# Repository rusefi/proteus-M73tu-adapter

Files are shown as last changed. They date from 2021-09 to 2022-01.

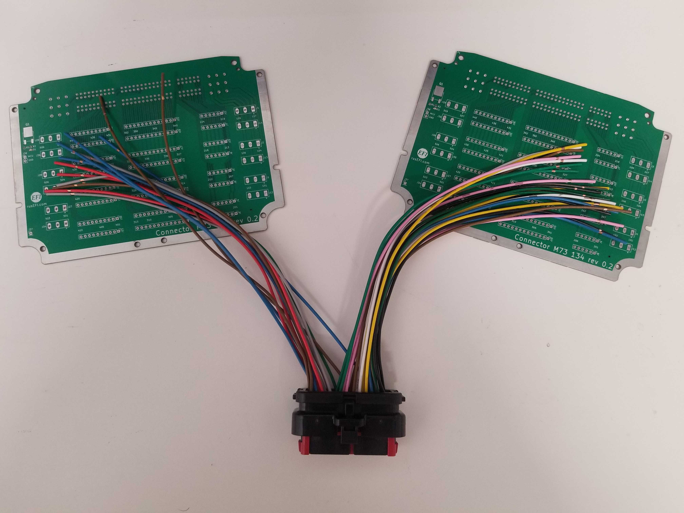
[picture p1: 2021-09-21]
todo/adapter-proto.jpg

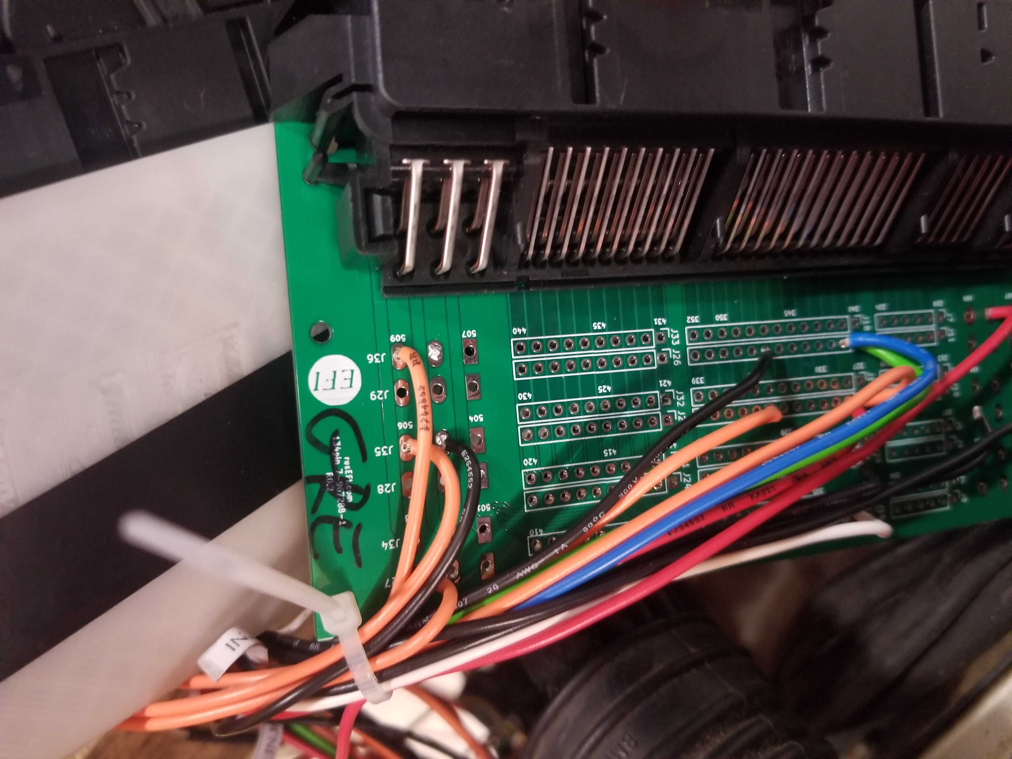
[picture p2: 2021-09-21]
todo/manual_wiring.jpg

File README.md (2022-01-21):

# proteus-m73tu-adapter

Part of https://github.com/rusefi/rusefi/wiki/Proteus#adapters family

https://github.com/mck1117/proteus meets https://github.com/rusefi/rusefi/wiki/HOWTO-M73-v12-on-Proteus

V12 harness uses _TWO_ 134 pin connectors - one with BLACK plugs another with GREY plugs.

x

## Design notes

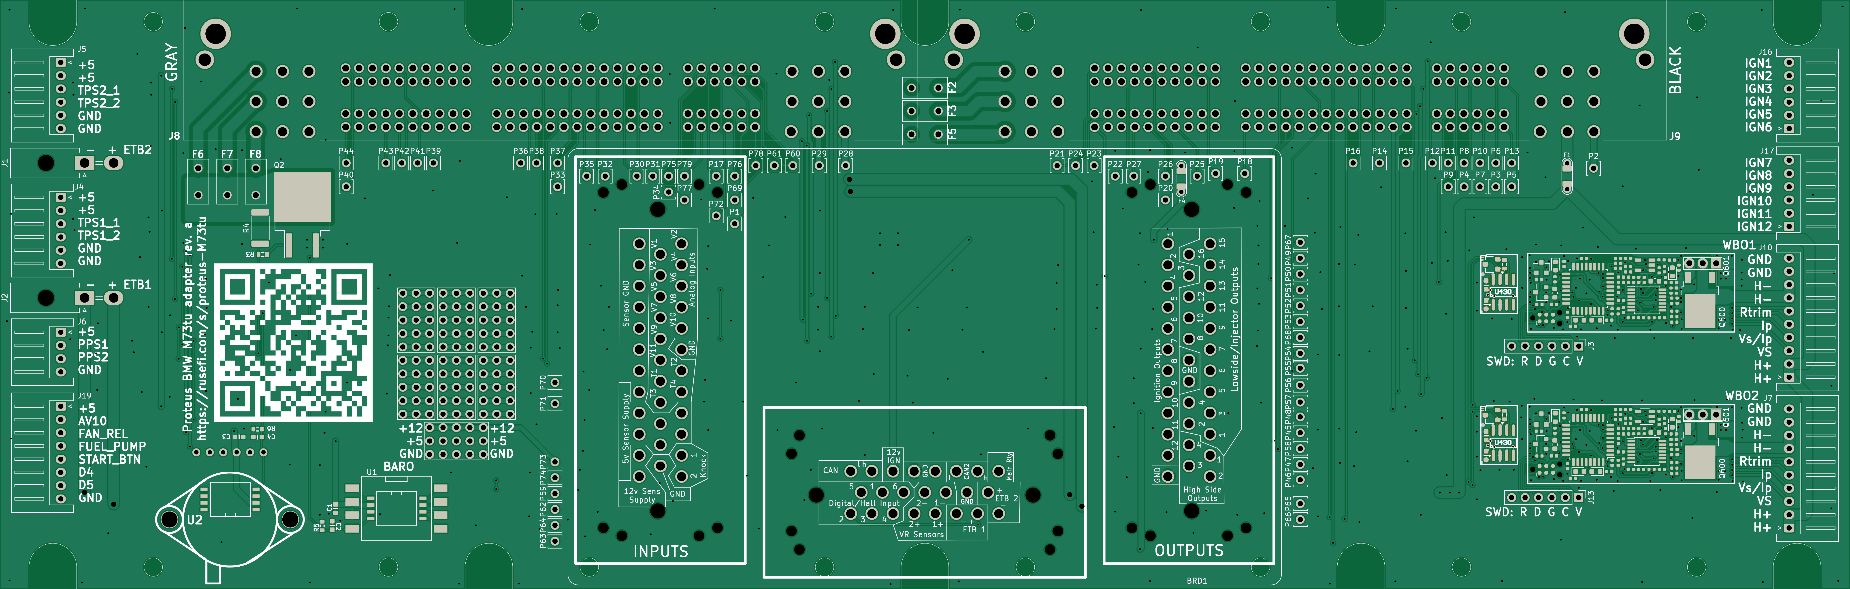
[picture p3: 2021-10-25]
proteusM73tu/boards/proteusM73tu-a/board/misc/proteusM73tu-a-top.png

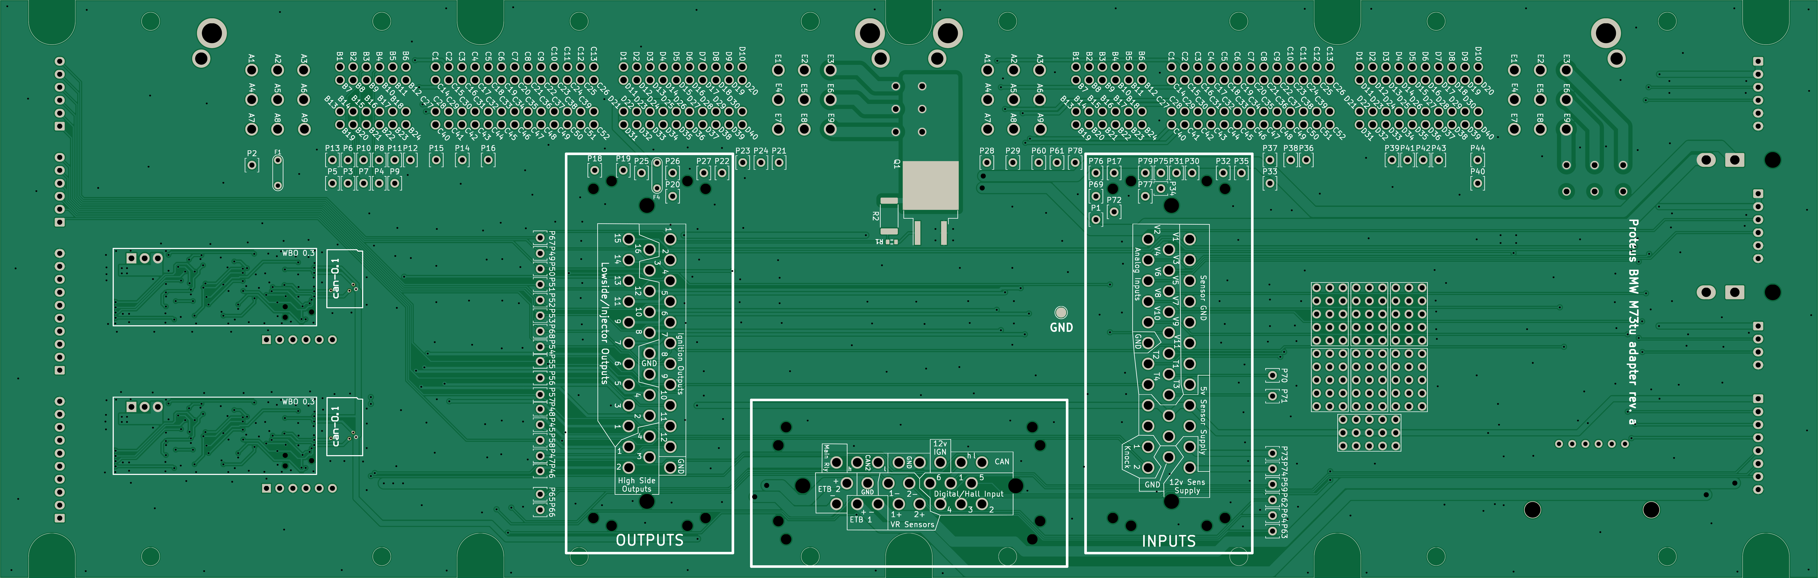
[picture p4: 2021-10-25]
proteusM73tu/boards/proteusM73tu-a/board/misc/proteusM73tu-a-bottom.png

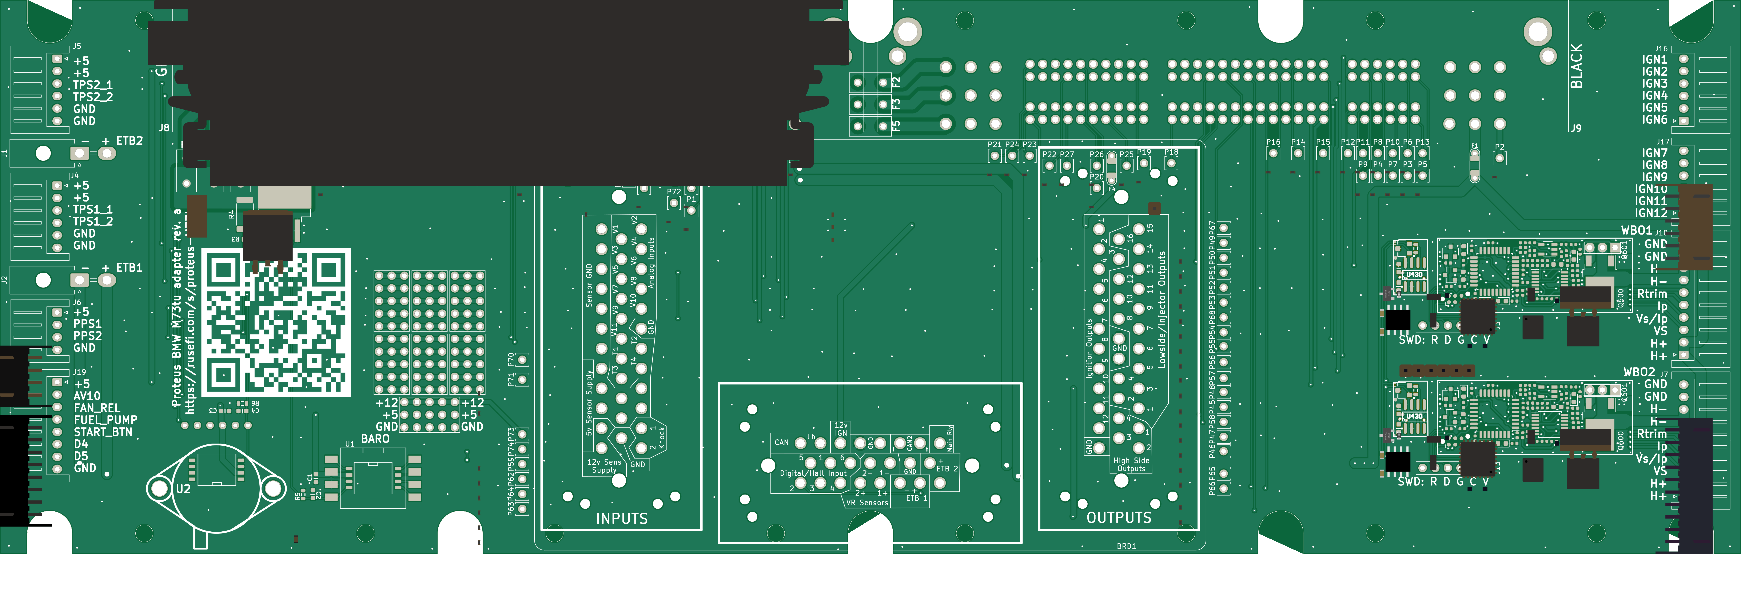
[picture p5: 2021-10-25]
proteusM73tu/boards/proteusM73tu-a/board/proteusM73tu-a.png

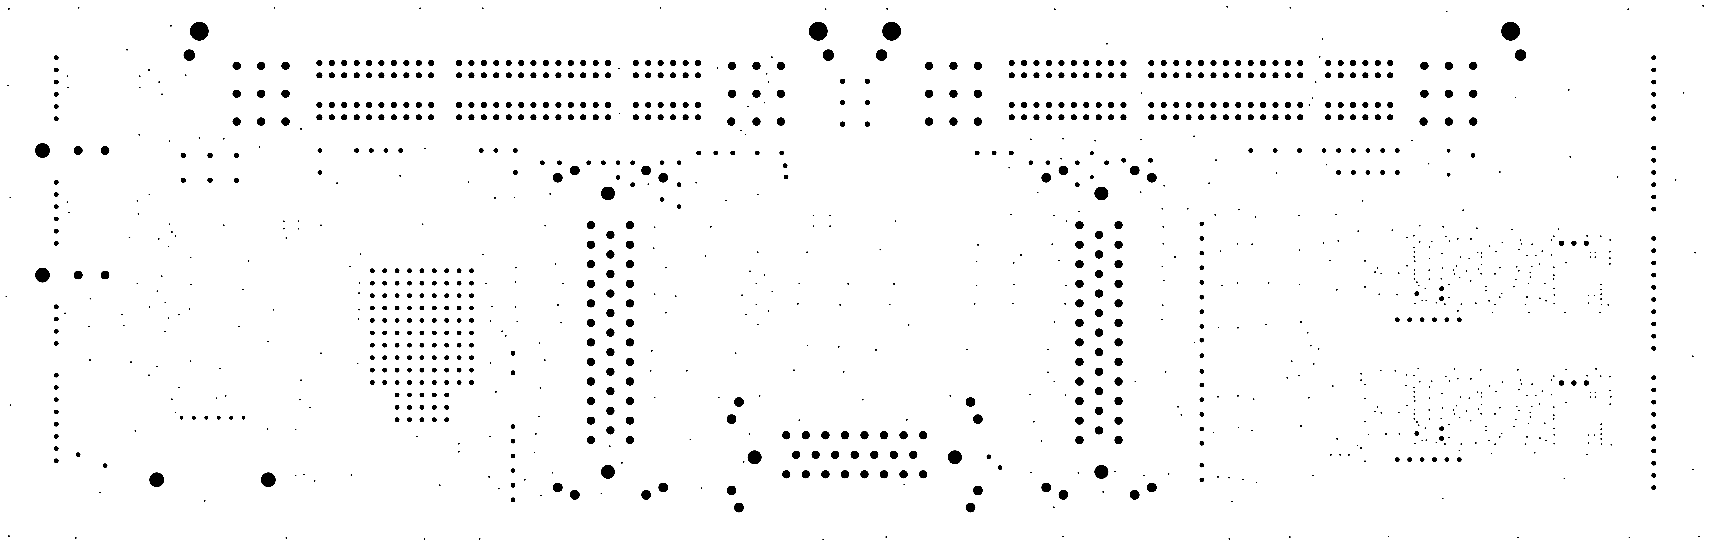
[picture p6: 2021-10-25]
proteusM73tu/boards/proteusM73tu-a/board/misc/proteusM73tu-a-outline.png

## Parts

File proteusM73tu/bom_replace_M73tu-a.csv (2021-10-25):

#WBO low-side (D2PAK | TO220)
Q600
Q600_2
Q601
Q601_2
#WBO STM32
U602
U602_2
#IGN IGBT
Q1 | ISL9V3040D3ST | DPAK | NON-JLC
Q2 | ISL9V3040D3ST | DPAK | NON-JLC
#MPX | MAP
U1
U2

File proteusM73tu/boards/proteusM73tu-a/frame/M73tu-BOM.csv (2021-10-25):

Comment | Designator | Footprint | LCSC Part #
proteus | BRD1 | proteus
100n | C1 | C0603 | C14663
47p | C2 | C0603 | C1671
100n | C3 | C0603 | C14663
47p | C4 | C0603 | C1671
Fuse-Pad-Pad | F1 | PAD-1206-PAD | C182446
10A | F2 | FUSE_8.5x4 | C354908
10A | F3 | FUSE_8.5x4 | C354908
Fuse-Pad-Pad | F4 | PAD-1206-PAD | C182446
10A | F5 | FUSE_8.5x4 | C354908
10A | F6 | FUSE_8.5x4 | C354908
10A | F7 | FUSE_8.5x4 | C354908
10A | F8 | FUSE_8.5x4 | C354908
PROTO_AREA | G1 | PROTO_AREA
PROTO_AREA | G2 | PROTO_AREA
PROTO_AREA | G3 | PROTO_AREA
PROTO_AREA | G4 | PROTO_AREA
PROTO_AREA | G5 | PROTO_AREA
PROTO_AREA | G6 | PROTO_AREA
PROTO_AREA | G7 | PROTO_AREA
Conn_01x02 | J1 | Molex_Mini-Fit_Jr_5569-02A2_2x01_P4.20mm_Horizontal | C240832
Conn_01x02 | J2 | Molex_Mini-Fit_Jr_5569-02A2_2x01_P4.20mm_Horizontal | C240832
Conn_01x06 | J3 | PinHeader_1x06_P2.54mm_Vertical
XH-6AW | J4 | JST_XH_S6B-XH-A_1x06_P2.50mm_Horizontal | C8876
XH-6AW | J5 | JST_XH_S6B-XH-A_1x06_P2.50mm_Horizontal | C8876
XH-4AW | J6 | JST_XH_S4B-XH-A_1x04_P2.50mm_Horizontal | C21273
XH-10AW | J7 | JST_XH_S10B-XH-A_1x10_P2.50mm_Horizontal | C14652
7-967288-1 | J8 | TE_7-967288-1
7-967288-1 | J9 | TE_7-967288-1
XH-10AW | J10 | JST_XH_S10B-XH-A_1x10_P2.50mm_Horizontal | C14652
Conn_01x06 | J13 | PinHeader_1x06_P2.54mm_Vertical
XH-6AW | J16 | JST_XH_S6B-XH-A_1x06_P2.50mm_Horizontal | C8876
XH-6AW | J17 | JST_XH_S6B-XH-A_1x06_P2.50mm_Horizontal | C8876
XH-8AW | J19 | JST_XH_S8B-XH-A_1x08_P2.50mm_Horizontal | C10395
Conn_01x01 | J20 | TestPoint_Pad_D2.0mm
Module:wbo/0.3 | M1 | wbo
Module:can/0.1 | M2 | can
Module:wbo/0.3 | M3 | wbo
Module:can/0.1 | M4 | can
Pad | P1 | PAD-TH
Pad | P2 | PAD-TH
Pad | P3 | PAD-TH
Pad | P4 | PAD-TH
Pad | P5 | PAD-TH
Pad | P6 | PAD-TH
Pad | P7 | PAD-TH
Pad | P8 | PAD-TH
Pad | P9 | PAD-TH
Pad | P10 | PAD-TH
Pad | P11 | PAD-TH
Pad | P12 | PAD-TH
Pad | P13 | PAD-TH
Pad | P14 | PAD-TH
Pad | P15 | PAD-TH
Pad | P16 | PAD-TH
Pad | P17 | PAD-TH
Pad | P18 | PAD-TH
Pad | P19 | PAD-TH
Pad | P20 | PAD-TH
Pad | P21 | PAD-TH
Pad | P22 | PAD-TH
Pad | P23 | PAD-TH
Pad | P24 | PAD-TH
Pad | P25 | PAD-TH
Pad | P26 | PAD-TH
Pad | P27 | PAD-TH
Pad | P28 | PAD-TH
Pad | P29 | PAD-TH
Pad | P30 | PAD-TH
Pad | P31 | PAD-TH
Pad | P32 | PAD-TH
Pad | P33 | PAD-TH
Pad | P34 | PAD-TH
Pad | P35 | PAD-TH
Pad | P36 | PAD-TH
Pad | P37 | PAD-TH
Pad | P38 | PAD-TH
Pad | P39 | PAD-TH
Pad | P40 | PAD-TH
Pad | P41 | PAD-TH
Pad | P42 | PAD-TH
Pad | P43 | PAD-TH
Pad | P44 | PAD-TH
Pad | P45 | PAD-TH
Pad | P46 | PAD-TH
Pad | P47 | PAD-TH
Pad | P48 | PAD-TH
Pad | P49 | PAD-TH
Pad | P50 | PAD-TH
Pad | P51 | PAD-TH
Pad | P52 | PAD-TH
Pad | P53 | PAD-TH
Pad | P54 | PAD-TH
Pad | P55 | PAD-TH
Pad | P56 | PAD-TH
Pad | P57 | PAD-TH
Pad | P58 | PAD-TH
Pad | P59 | PAD-TH
Pad | P60 | PAD-TH
Pad | P61 | PAD-TH
Pad | P62 | PAD-TH
Pad | P63 | PAD-TH
Pad | P64 | PAD-TH
Pad | P65 | PAD-TH
Pad | P66 | PAD-TH
Pad | P67 | PAD-TH
Pad | P68 | PAD-TH
Pad | P69 | PAD-TH
Pad | P70 | PAD-TH
Pad | P71 | PAD-TH
Pad | P72 | PAD-TH
Pad | P73 | PAD-TH
Pad | P74 | PAD-TH
Pad | P75 | PAD-TH
Pad | P76 | PAD-TH
Pad | P77 | PAD-TH
Pad | P78 | PAD-TH
Pad | P79 | PAD-TH
ISL9V3040S3S | Q1 | TO-263-2 | C898702
ISL9V3040S3S | Q2 | TO-263-2 | C898702
22 | R1 | R0603 | C23345
DNP | R2 | R_2512_6332Metric
22 | R3 | R0603 | C23345
DNP | R4 | R_2512_6332Metric
51k | R5 | R0603 | C23196
51k | R6 | R0603 | C23196
MPXxx6115A | U1 | MPX_SOP_SSOP
MPX4/MPXH6400_MAP | U2 | MPX-4_MAP

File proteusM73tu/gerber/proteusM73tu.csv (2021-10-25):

Comment | Designator | Footprint | LCSC Part #
proteus | BRD1 | kicad6-libraries:proteus
100n | C1 | hellen-one-common:C0603 | C14663
47p | C2 | hellen-one-common:C0603 | C1671
100n | C3 | hellen-one-common:C0603 | C14663
47p | C4 | hellen-one-common:C0603 | C1671
Fuse-Pad-Pad | F1 | hellen-one-common:PAD-1206-PAD | C182446
10A | F2 | kicad6-libraries:FUSE_8.5x4 | C354908
10A | F3 | kicad6-libraries:FUSE_8.5x4 | C354908
Fuse-Pad-Pad | F4 | hellen-one-common:PAD-1206-PAD | C182446
10A | F5 | kicad6-libraries:FUSE_8.5x4 | C354908
10A | F6 | kicad6-libraries:FUSE_8.5x4 | C354908
10A | F7 | kicad6-libraries:FUSE_8.5x4 | C354908
10A | F8 | kicad6-libraries:FUSE_8.5x4 | C354908
PROTO_AREA | G1 | hellen-one-common:PROTO_AREA
PROTO_AREA | G2 | hellen-one-common:PROTO_AREA
PROTO_AREA | G3 | hellen-one-common:PROTO_AREA
PROTO_AREA | G4 | hellen-one-common:PROTO_AREA
PROTO_AREA | G5 | hellen-one-common:PROTO_AREA
PROTO_AREA | G6 | hellen-one-common:PROTO_AREA
PROTO_AREA | G7 | hellen-one-common:PROTO_AREA
Conn_01x02 | J1 | Connector_Molex:Molex_Mini-Fit_Jr_5569-02A2_2x01_P4.20mm_Horizontal | C240832
Conn_01x02 | J2 | Connector_Molex:Molex_Mini-Fit_Jr_5569-02A2_2x01_P4.20mm_Horizontal | C240832
Conn_01x06 | J3 | Connector_PinHeader_2.54mm:PinHeader_1x06_P2.54mm_Vertical
XH-6AW | J4 | Connector_JST:JST_XH_S6B-XH-A_1x06_P2.50mm_Horizontal | C8876
XH-6AW | J5 | Connector_JST:JST_XH_S6B-XH-A_1x06_P2.50mm_Horizontal | C8876
XH-4AW | J6 | Connector_JST:JST_XH_S4B-XH-A_1x04_P2.50mm_Horizontal | C21273
XH-10AW | J7 | Connector_JST:JST_XH_S10B-XH-A_1x10_P2.50mm_Horizontal | C14652
7-967288-1 | J8 | kicad6-libraries:TE_7-967288-1
7-967288-1 | J9 | kicad6-libraries:TE_7-967288-1
XH-10AW | J10 | Connector_JST:JST_XH_S10B-XH-A_1x10_P2.50mm_Horizontal | C14652
Conn_01x06 | J13 | Connector_PinHeader_2.54mm:PinHeader_1x06_P2.54mm_Vertical
XH-6AW | J16 | Connector_JST:JST_XH_S6B-XH-A_1x06_P2.50mm_Horizontal | C8876
XH-6AW | J17 | Connector_JST:JST_XH_S6B-XH-A_1x06_P2.50mm_Horizontal | C8876
XH-8AW | J19 | Connector_JST:JST_XH_S8B-XH-A_1x08_P2.50mm_Horizontal | C10395
Conn_01x01 | J20 | TestPoint:TestPoint_Pad_D2.0mm
Module-wbo-0.3 | M1 | hellen-one-wbo-0.3:wbo
Module-can-0.1 | M2 | hellen-one-can-0.1:can
Module-wbo-0.3 | M3 | hellen-one-wbo-0.3:wbo
Module-can-0.1 | M4 | hellen-one-can-0.1:can
Pad | P1 | hellen-one-common:PAD-TH
Pad | P2 | hellen-one-common:PAD-TH
Pad | P3 | hellen-one-common:PAD-TH
Pad | P4 | hellen-one-common:PAD-TH
Pad | P5 | hellen-one-common:PAD-TH
Pad | P6 | hellen-one-common:PAD-TH
Pad | P7 | hellen-one-common:PAD-TH
Pad | P8 | hellen-one-common:PAD-TH
Pad | P9 | hellen-one-common:PAD-TH
Pad | P10 | hellen-one-common:PAD-TH
Pad | P11 | hellen-one-common:PAD-TH
Pad | P12 | hellen-one-common:PAD-TH
Pad | P13 | hellen-one-common:PAD-TH
Pad | P14 | hellen-one-common:PAD-TH
Pad | P15 | hellen-one-common:PAD-TH
Pad | P16 | hellen-one-common:PAD-TH
Pad | P17 | hellen-one-common:PAD-TH
Pad | P18 | hellen-one-common:PAD-TH
Pad | P19 | hellen-one-common:PAD-TH
Pad | P20 | hellen-one-common:PAD-TH
Pad | P21 | hellen-one-common:PAD-TH
Pad | P22 | hellen-one-common:PAD-TH
Pad | P23 | hellen-one-common:PAD-TH
Pad | P24 | hellen-one-common:PAD-TH
Pad | P25 | hellen-one-common:PAD-TH
Pad | P26 | hellen-one-common:PAD-TH
Pad | P27 | hellen-one-common:PAD-TH
Pad | P28 | hellen-one-common:PAD-TH
Pad | P29 | hellen-one-common:PAD-TH
Pad | P30 | hellen-one-common:PAD-TH
Pad | P31 | hellen-one-common:PAD-TH
Pad | P32 | hellen-one-common:PAD-TH
Pad | P33 | hellen-one-common:PAD-TH
Pad | P34 | hellen-one-common:PAD-TH
Pad | P35 | hellen-one-common:PAD-TH
Pad | P36 | hellen-one-common:PAD-TH
Pad | P37 | hellen-one-common:PAD-TH
Pad | P38 | hellen-one-common:PAD-TH
Pad | P39 | hellen-one-common:PAD-TH
Pad | P40 | hellen-one-common:PAD-TH
Pad | P41 | hellen-one-common:PAD-TH
Pad | P42 | hellen-one-common:PAD-TH
Pad | P43 | hellen-one-common:PAD-TH
Pad | P44 | hellen-one-common:PAD-TH
Pad | P45 | hellen-one-common:PAD-TH
Pad | P46 | hellen-one-common:PAD-TH
Pad | P47 | hellen-one-common:PAD-TH
Pad | P48 | hellen-one-common:PAD-TH
Pad | P49 | hellen-one-common:PAD-TH
Pad | P50 | hellen-one-common:PAD-TH
Pad | P51 | hellen-one-common:PAD-TH
Pad | P52 | hellen-one-common:PAD-TH
Pad | P53 | hellen-one-common:PAD-TH
Pad | P54 | hellen-one-common:PAD-TH
Pad | P55 | hellen-one-common:PAD-TH
Pad | P56 | hellen-one-common:PAD-TH
Pad | P57 | hellen-one-common:PAD-TH
Pad | P58 | hellen-one-common:PAD-TH
Pad | P59 | hellen-one-common:PAD-TH
Pad | P60 | hellen-one-common:PAD-TH
Pad | P61 | hellen-one-common:PAD-TH
Pad | P62 | hellen-one-common:PAD-TH
Pad | P63 | hellen-one-common:PAD-TH
Pad | P64 | hellen-one-common:PAD-TH
Pad | P65 | hellen-one-common:PAD-TH
Pad | P66 | hellen-one-common:PAD-TH
Pad | P67 | hellen-one-common:PAD-TH
Pad | P68 | hellen-one-common:PAD-TH
Pad | P69 | hellen-one-common:PAD-TH
Pad | P70 | hellen-one-common:PAD-TH
Pad | P71 | hellen-one-common:PAD-TH
Pad | P72 | hellen-one-common:PAD-TH
Pad | P73 | hellen-one-common:PAD-TH
Pad | P74 | hellen-one-common:PAD-TH
Pad | P75 | hellen-one-common:PAD-TH
Pad | P76 | hellen-one-common:PAD-TH
Pad | P77 | hellen-one-common:PAD-TH
Pad | P78 | hellen-one-common:PAD-TH
Pad | P79 | hellen-one-common:PAD-TH
ISL9V3040S3S | Q1 | Package_TO_SOT_SMD:TO-263-2 | C898702
ISL9V3040S3S | Q2 | Package_TO_SOT_SMD:TO-263-2 | C898702
22 | R1 | hellen-one-common:R0603 | C23345
DNP | R2 | Resistor_SMD:R_2512_6332Metric
22 | R3 | hellen-one-common:R0603 | C23345
DNP | R4 | Resistor_SMD:R_2512_6332Metric
51k | R5 | hellen-one-common:R0603 | C23196
51k | R6 | hellen-one-common:R0603 | C23196
MPXxx6115A | U1 | kicad6-libraries:MPX_SOP_SSOP
MPX4/MPXH6400_MAP | U2 | kicad6-libraries:MPX-4_MAP

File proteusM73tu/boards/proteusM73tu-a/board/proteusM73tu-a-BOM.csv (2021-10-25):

Comment | Designator | Footprint | LCSC Part #
proteus | BRD1 | proteus
100n | C1, C3, C430, C431, C430_2, C431_2 | C0603 | C14663
47p | C2, C4 | C0603 | C1671
Fuse-Pad-Pad | F1, F4 | PAD-1206-PAD | C182446
10A | F2, F3, F5, F6, F7, F8 | FUSE_8.5x4 | C354908
PROTO_AREA | G1 | PROTO_AREA
PROTO_AREA | G2 | PROTO_AREA
PROTO_AREA | G3 | PROTO_AREA
PROTO_AREA | G4 | PROTO_AREA
PROTO_AREA | G5 | PROTO_AREA
PROTO_AREA | G6 | PROTO_AREA
PROTO_AREA | G7 | PROTO_AREA
Conn_01x02 | J1, J2 | Molex_Mini-Fit_Jr_5569-02A2_2x01_P4.20mm_Horizontal | C240832
Conn_01x06 | J3 | PinHeader_1x06_P2.54mm_Vertical
XH-6AW | J4, J5, J16, J17 | JST_XH_S6B-XH-A_1x06_P2.50mm_Horizontal | C8876
XH-4AW | J6 | JST_XH_S4B-XH-A_1x04_P2.50mm_Horizontal | C21273
XH-10AW | J7, J10 | JST_XH_S10B-XH-A_1x10_P2.50mm_Horizontal | C14652
7-967288-1 | J8 | TE_7-967288-1
7-967288-1 | J9 | TE_7-967288-1
Conn_01x06 | J13 | PinHeader_1x06_P2.54mm_Vertical
XH-8AW | J19 | JST_XH_S8B-XH-A_1x08_P2.50mm_Horizontal | C10395
Conn_01x01 | J20 | TestPoint_Pad_D2.0mm
Pad | P1 | PAD-TH
Pad | P2 | PAD-TH
Pad | P3 | PAD-TH
Pad | P4 | PAD-TH
Pad | P5 | PAD-TH
Pad | P6 | PAD-TH
Pad | P7 | PAD-TH
Pad | P8 | PAD-TH
Pad | P9 | PAD-TH
Pad | P10 | PAD-TH
Pad | P11 | PAD-TH
Pad | P12 | PAD-TH
Pad | P13 | PAD-TH
Pad | P14 | PAD-TH
Pad | P15 | PAD-TH
Pad | P16 | PAD-TH
Pad | P17 | PAD-TH
Pad | P18 | PAD-TH
Pad | P19 | PAD-TH
Pad | P20 | PAD-TH
Pad | P21 | PAD-TH
Pad | P22 | PAD-TH
Pad | P23 | PAD-TH
Pad | P24 | PAD-TH
Pad | P25 | PAD-TH
Pad | P26 | PAD-TH
Pad | P27 | PAD-TH
Pad | P28 | PAD-TH
Pad | P29 | PAD-TH
Pad | P30 | PAD-TH
Pad | P31 | PAD-TH
Pad | P32 | PAD-TH
Pad | P33 | PAD-TH
Pad | P34 | PAD-TH
Pad | P35 | PAD-TH
Pad | P36 | PAD-TH
Pad | P37 | PAD-TH
Pad | P38 | PAD-TH
Pad | P39 | PAD-TH
Pad | P40 | PAD-TH
Pad | P41 | PAD-TH
Pad | P42 | PAD-TH
Pad | P43 | PAD-TH
Pad | P44 | PAD-TH
Pad | P45 | PAD-TH
Pad | P46 | PAD-TH
Pad | P47 | PAD-TH
Pad | P48 | PAD-TH
Pad | P49 | PAD-TH
Pad | P50 | PAD-TH
Pad | P51 | PAD-TH
Pad | P52 | PAD-TH
Pad | P53 | PAD-TH
Pad | P54 | PAD-TH
Pad | P55 | PAD-TH
Pad | P56 | PAD-TH
Pad | P57 | PAD-TH
Pad | P58 | PAD-TH
Pad | P59 | PAD-TH
Pad | P60 | PAD-TH
Pad | P61 | PAD-TH
Pad | P62 | PAD-TH
Pad | P63 | PAD-TH
Pad | P64 | PAD-TH
Pad | P65 | PAD-TH
Pad | P66 | PAD-TH
Pad | P67 | PAD-TH
Pad | P68 | PAD-TH
Pad | P69 | PAD-TH
Pad | P70 | PAD-TH
Pad | P71 | PAD-TH
Pad | P72 | PAD-TH
Pad | P73 | PAD-TH
Pad | P74 | PAD-TH
Pad | P75 | PAD-TH
Pad | P76 | PAD-TH
Pad | P77 | PAD-TH
Pad | P78 | PAD-TH
Pad | P79 | PAD-TH
22 | R1, R3 | R0603 | C23345
DNP | R2 | R_2512_6332Metric
DNP | R4 | R_2512_6332Metric
51k | R5, R6 | R0603 | C23196
1u | C600, C607, C609, C610, C611, C600_2, C607_2, C609_2, C610_2, C611_2 | C0402 | C52923
100n | C601, C602, C605, C608, C612, C613, C614, C615, C601_2, C602_2, C605_2, C608_2, C612_2, C613_2, C614_2, C615_2 | C0402 | C1525
33n | C603, C603_2 | C0402 | C1585
DNP | C604 | C0402
DNP | C606 | C0402
4.7u | C616, C616_2 | C0603 | C19666
LED-RED-0603 | D600, D603, D600_2, D603_2 | LED-0603 | C2286
LED-GREEN-0603 | D601, D601_2 | LED-0603 | C72043
LED-BLUE-0603 | D602, D602_2 | LED-0603 | C72041
1k | R600, R601, R616, R617, R622, R626, R627, R628, R600_2, R601_2, R616_2, R617_2, R622_2, R626_2, R627_2, R628_2 | R0402 | C11702
68k | R602, R603, R602_2, R603_2 | R0402 | C36871
10k | R604, R605, R613, R614, R618, R619, R625, R604_2, R605_2, R613_2, R614_2, R618_2, R619_2, R625_2 | R0402 | C25744
10 | R606, R606_2 | R0402 | C25077
22k | R607, R607_2 | R0402 | C25768
47 | R608, R608_2 | R0402 | C25118
61.9 | R609, R609_2 | R0603 | C23092
20k | R610, R611, R612, R610_2, R611_2, R612_2 | R0402 | C25765
100k | R615, R621, R615_2, R621_2 | R0402 | C25741
27k | R620, R623, R620_2, R623_2 | R0402 | C25771
3.3k | R624, R624_2 | R0402 | C25890
MCP6004 | U600, U600_2 | TSSOP14 | C50282
AD8628 | U601, U601_2 | TSOT23-5 | C29309
REF3033 | U603, U603_2 | SOT-23 | C36658
XC6206P332MR | U604, U604_2 | SOT-23 | C5446
PESD1CAN | D430, D430_2 | SOT-23 | C343993
120 | R430, R430_2 | R0603 | C22787
TJA1051T/3/1J | U430, U430_2 | SO8 | C38695
DNP | C604_2 | C0402
DNP | C606_2 | C0402
ISL9V3040D3ST | Q1, Q2 | DPAK | NON-JLC

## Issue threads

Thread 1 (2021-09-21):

Fix igniter

rusefillc, 2021-09-21:
not our favorite igniter?

also looks like things are very broken with schematics

Qwerty-OFF, 2021-10-04:
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

rusefillc, 2021-10-04:
let's put a via on A35 and A30 traces

We actually need two of same 6 pos "white" headers on these IGN traces for smart coil conversion

Closed 2021-11-05.

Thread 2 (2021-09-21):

Each adapter board solder point to have ampseal pin number on silkscreen

rusefillc, 2021-09-21:
are we making two separate PCBs "black" and "grey" or do we design same exact PCB with both "black" and "grey" version of the silkscreen at the same time

Closed 2021-11-05.

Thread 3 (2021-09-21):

all pins not used by amp-seal connectors should still be accessible

rusefillc, 2021-09-21:
one hole per connector pad would be enough if that helps.

please enlarge wire hole diameter by 15%

Closed 2021-11-05.

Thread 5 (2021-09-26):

Data readiness

rusefillc, 2021-09-26:
This ticket should be assigned to @rusefillc if data input is needed

This ticket should be assigned NOT to @rusefillc if we have data to move forward

rusefillc, 2021-09-26:
Please place two 134 footprints on the schematics and I will work on pinout data entry

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

rusefillc, 2021-09-29:
@Timbelom has entered some basic data

Qwerty-OFF, 2021-10-03:
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

rusefillc, 2021-10-03:
perfect

Closed 2021-11-05.

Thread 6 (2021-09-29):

dual-etb connectors and pedal connector

rusefillc, 2021-09-29:
We need dual ETB both high-current DC output and position sensors

We need single pedal position sensor connector

rusefillc, 2021-09-29:
Most interesting question is what connectors do we go with

NB1 suggests C240832 for DC motors

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

Qwerty-OFF, 2021-10-04:
C240832 for ETB
C8876 for TPS
C21273 for PPS
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

Closed 2021-10-04.

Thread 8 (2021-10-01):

MAP sensor

rusefillc, 2021-10-01:
BMW does not have OEM MAP sensor so we shall add on the adapter

Please attempt a dual footprint: MPX4250 like used on Miata is getting harder to purchase, please add MPXH6400 as second option

need "MAP" silkscreen to distinguish from BARO

(Honda has OEM MAP sensor)

rusefillc, 2021-10-04:
only one would be soldred on any specific board so combined footprint would be best

Qwerty-OFF, 2021-10-04:
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

Closed 2021-10-04.

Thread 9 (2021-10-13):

enclosure options

rusefillc, 2021-10-13:
option 1
SERPAC 182
361 mm	124 mm	51 mm
124 mm too short to fit proteus or can we fit?

option 2
11.81 inch wide a bit narrow for two connectors side to side?

any of https://www.hammfg.com/electronics/small-case/plastic/1555#product-tables

Qwerty-OFF, 2021-10-20:
SEPARC 182
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
Trying making this board for this case?
Second option seems too small:
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

rusefillc, 2021-11-05:
@Qwerty-OFF can you please push 3D model of PCB + connectors (at least the 134 pin connectors but maybe also the Proteus connectors if that's trivial) but without case?

Qwerty-OFF, 2021-11-05:
Done https://github.com/rusefi/proteus-M73tu-adapter/commit/ae6f634b250771e12c39469326bce1ea650017fa

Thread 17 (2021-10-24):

Progress

rusefillc, 2021-10-24:
1. it's OK to have vias available for jumper wires only from the back

2. let's NOT have IGBT under Proteus - let's rather place it on the BACK

3. not great but acceptable, hopefully we are not planning to burn those often
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

4. let's SOLDER smaller IGBT like on bmw88 into LARGER igbt pad like

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

Closed 2021-11-05.

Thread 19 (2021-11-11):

Dual +5 vs Single +5 should be the other way around

rusefillc, 2021-11-11:
TPS are sensors within ETB body, 6 wires total - two wires for DC motors leaves 4 wires for sensor meaning single +5

PPS is pedal position sensor same 6 wires total but now dual +5v and dual GND

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

See also https://github.com/rusefi/rusefi/wiki/Vault-Of-Electronic-Throttle-Bodies-ETB for pictures and examples

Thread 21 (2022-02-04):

R1 should be larger

rusefillc, 2022-02-04:
R1 is on the back side and it's hand-soldered thus it should be physically larger part

Same R3 just for consistency

funny idea: we need not connected R999 on top side just for JLCPCB to mount a spare resistor for human to transfer on back side

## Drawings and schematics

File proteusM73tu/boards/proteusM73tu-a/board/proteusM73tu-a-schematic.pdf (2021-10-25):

# P28 P1 GND GND

# J18 XH-8A DNP

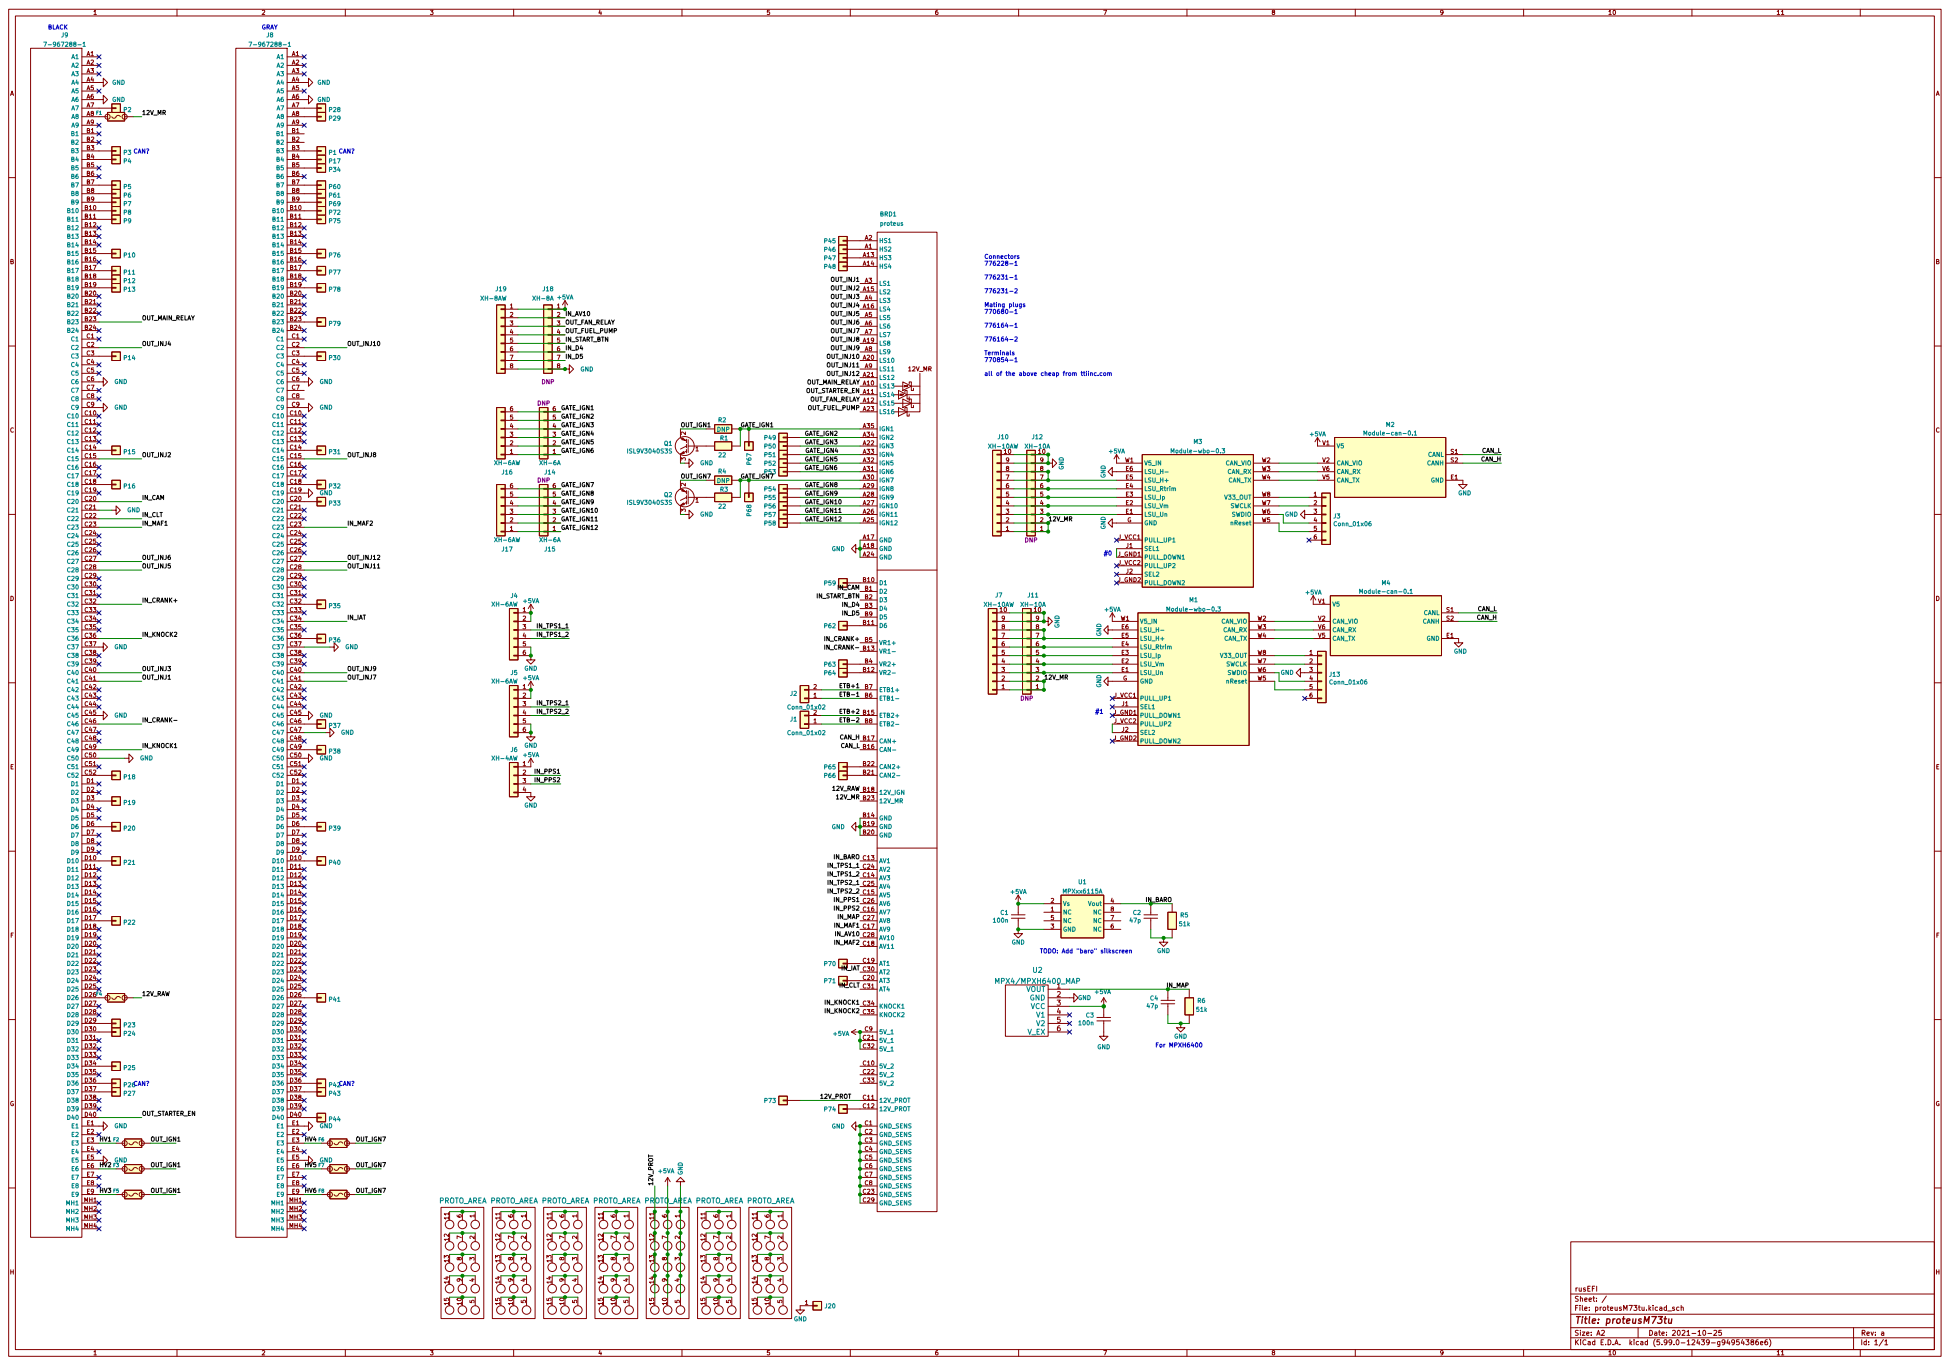
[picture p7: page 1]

all of the above cheap from ttiinc.com

1kR600

3.3k R623

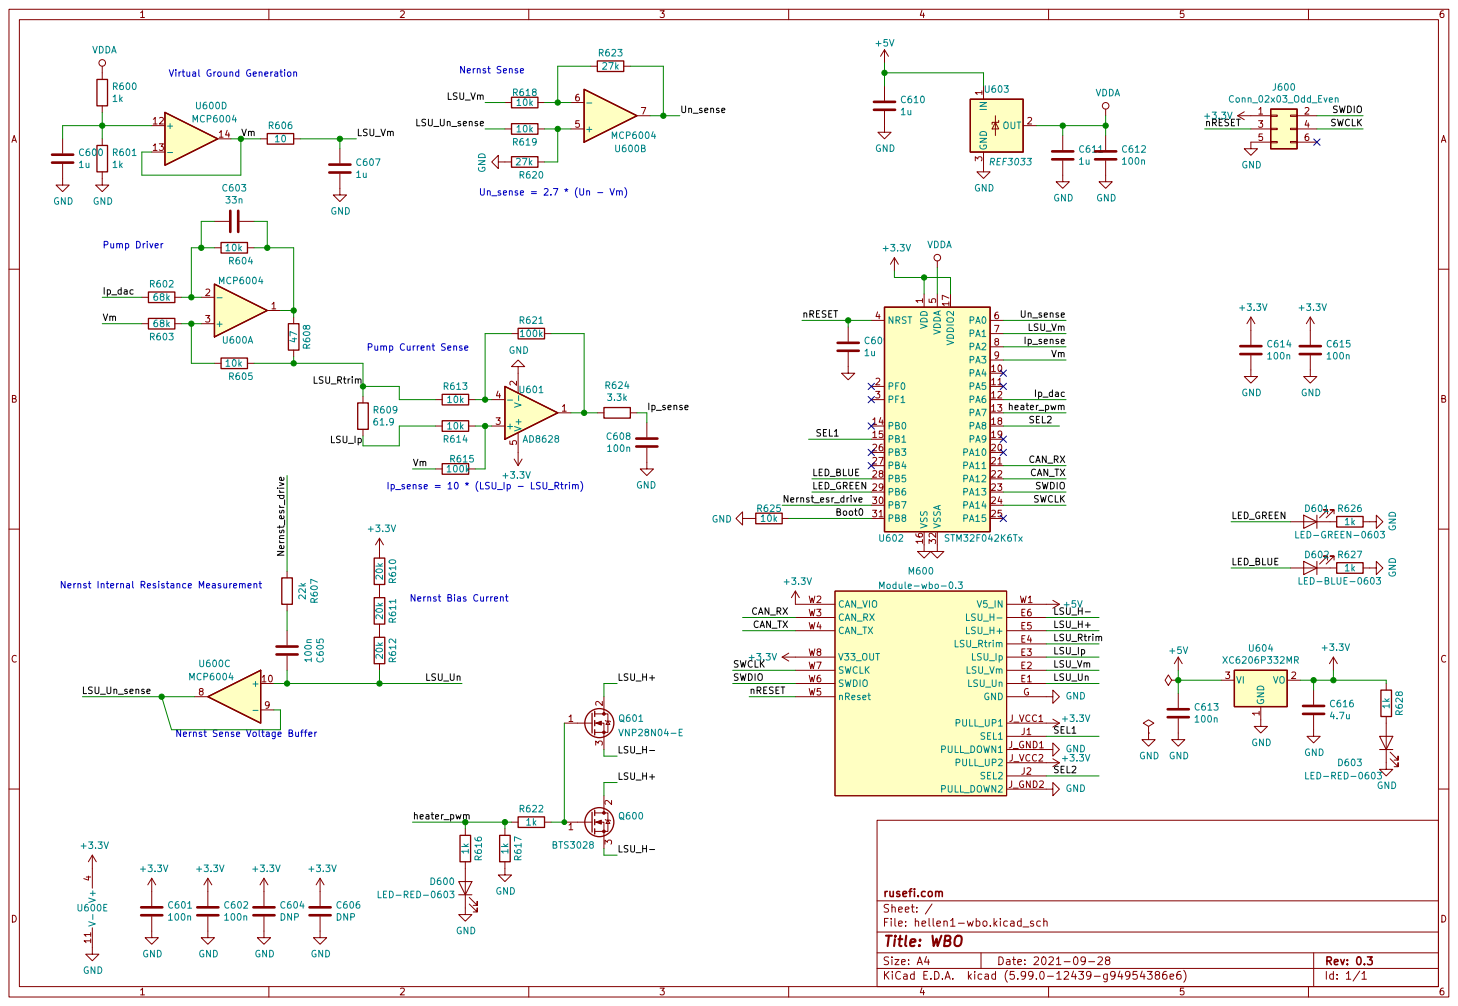
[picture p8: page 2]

Pump Current Sense Nernst Sense

LSU_Vm
Pump Driver Nernst Internal Resistance Measurement

1 VO 2 VI 3 U604 XC6206P332MR GND GND

1 PA4 10 PA5 11 PA6 12 PA7 13 PB0 14 PB1 15 VSS 16 VDDIO2 17 PA8 18 PA9 19 PF0 2 PA10 20 PA11 21 PA12 22 PA13 23 PA14 24 PA15 25 PB3 26 PB4 27 PB5 28 PB6 29 PF1 3 PB7 30 PB8 31 VSSA 32 NRST 4 VDDA

LED-RED-0603 ¹⁰⁰n C⁶⁰⁵ C604 DNP

Nernst Sense Voltage Buffer

1k GND GND R⁶¹⁶ ¹k

File: hellen1-wbo.kicad_sch Sheet: / rusefi.com

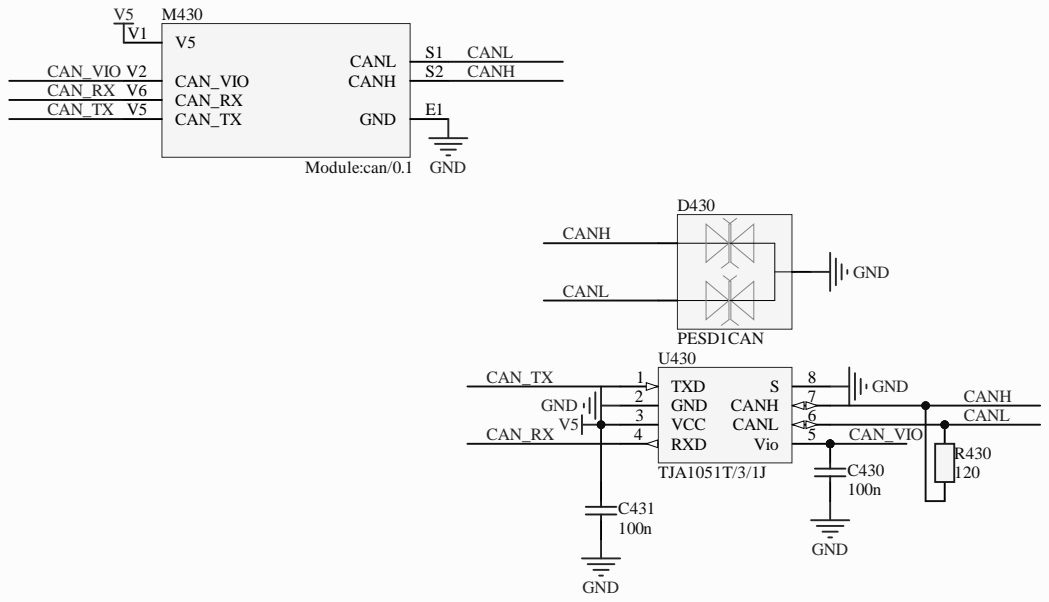
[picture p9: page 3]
andreika; Size:; Author:; Date:; Revision:; Sheet; PESD1CAN; GND; CANH; CANL; TXD 1 GND 2 VCC 3; Vio; 5 RXD 4; 6 CANH; TJA1051T/3/1J; CANH CANL; CAN_TX; CAN_RX; CAN_VIO; CAN_VIO V2; S2 CANL; CAN_TX V5; CAN_RX V6; Module:can/0.1

Hellen-One CAN
Title:

rusEFI EMS
Hellen-One Platform
https://rusefi.com/s/hellen72

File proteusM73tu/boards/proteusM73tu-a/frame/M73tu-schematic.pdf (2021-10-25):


all of the above cheap from ttiinc.com

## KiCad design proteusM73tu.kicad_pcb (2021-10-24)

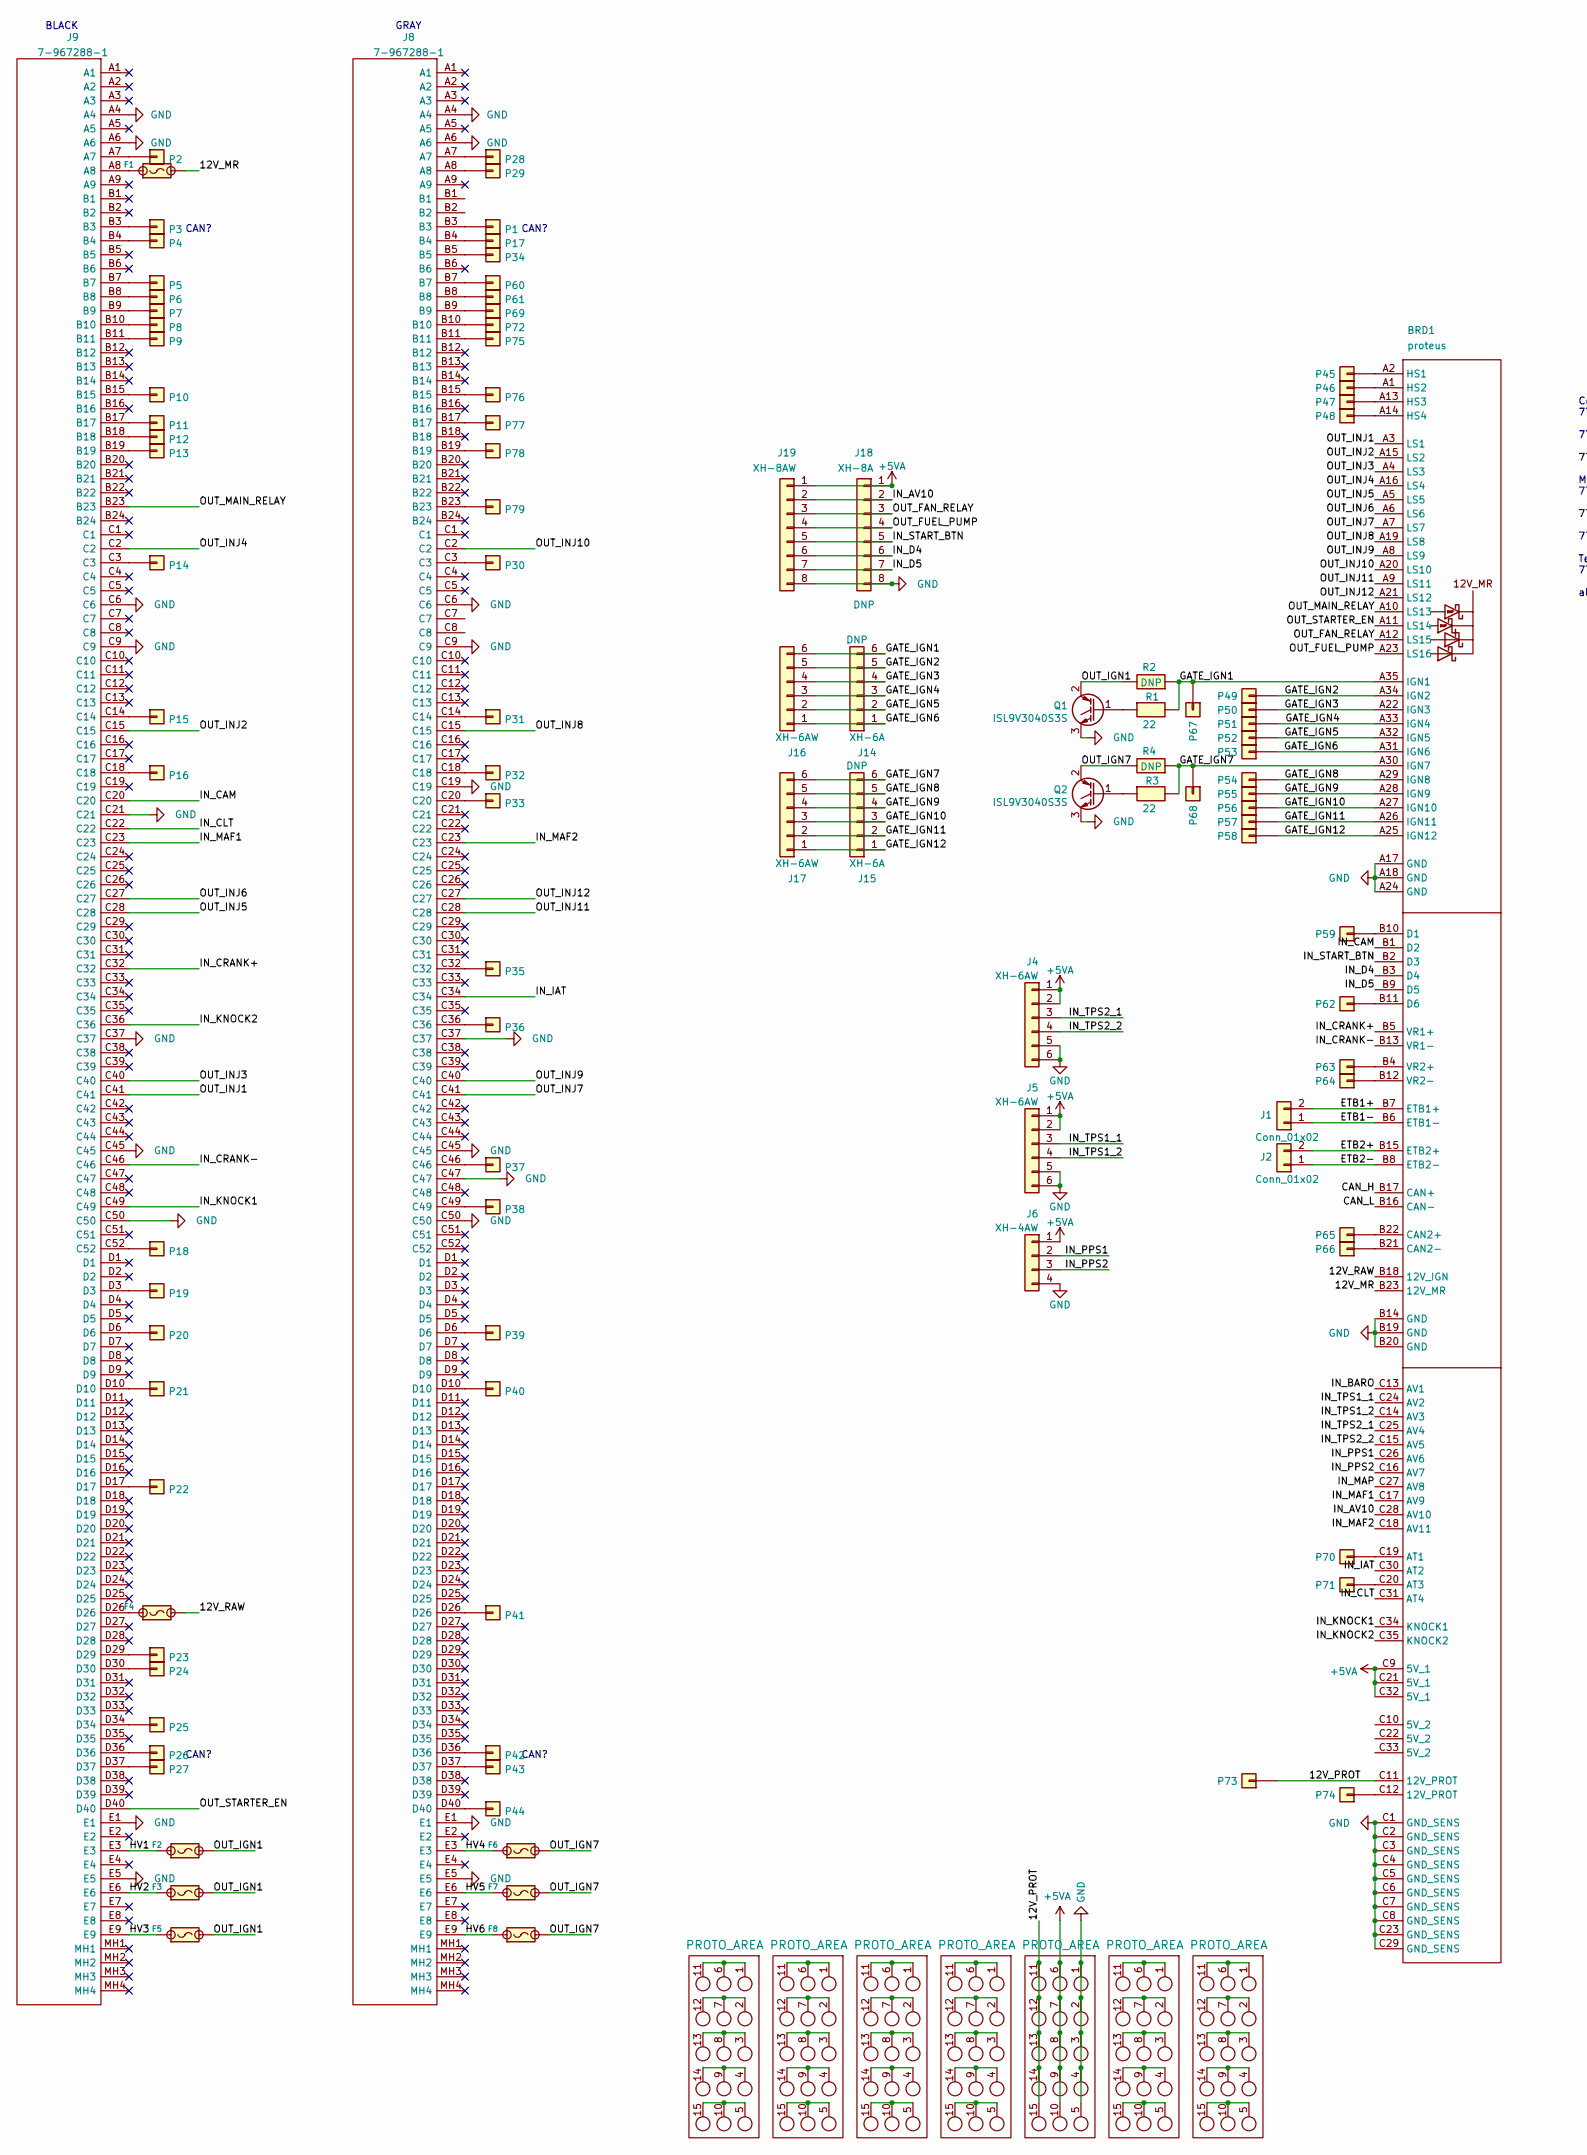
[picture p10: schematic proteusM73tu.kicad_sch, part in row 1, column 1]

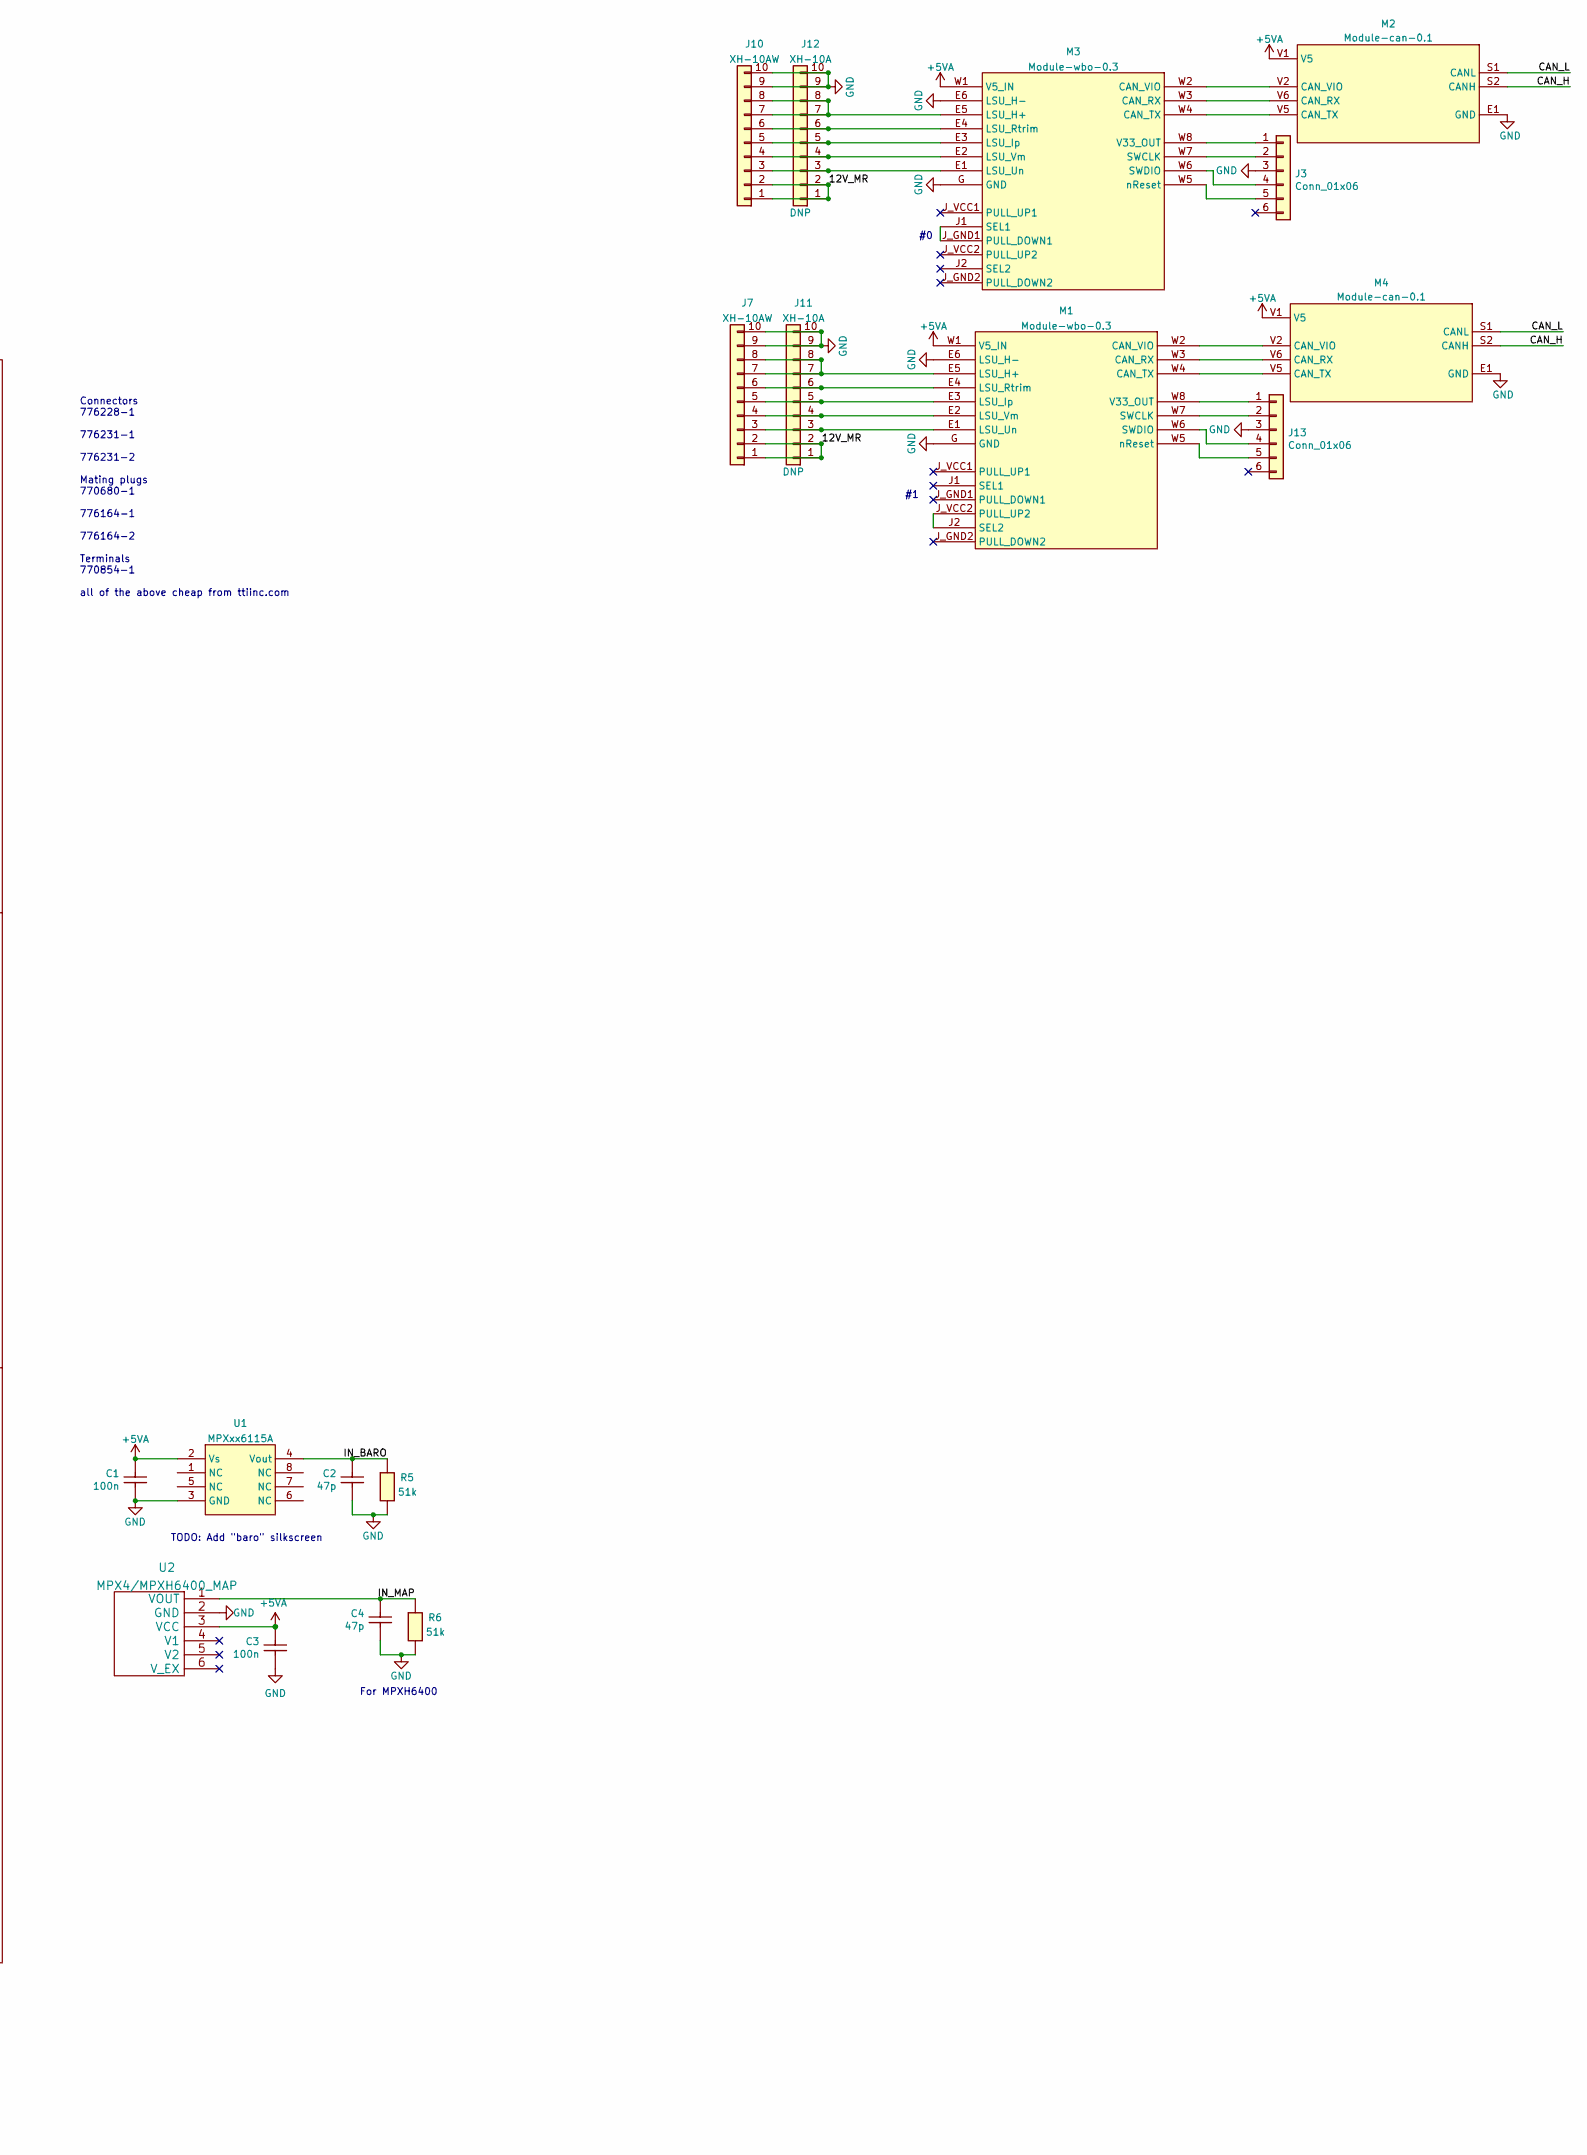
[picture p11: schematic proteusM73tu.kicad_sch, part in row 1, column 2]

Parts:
BRD1: proteus
C1, C3: 100n; C0603; LCSC C14663
C2, C4: 47p; C0603; LCSC C1671
F1, F4: Fuse-Pad-Pad; PAD-1206-PAD; LCSC C182446
F2, F3, F5, F6, F7, F8: 10A; FUSE_8.5x4; LCSC C354908
G1, G2, G3, G4, G5, G6, G7: PROTO_AREA
J1, J2: Conn_01x02; Molex_Mini-Fit_Jr_5569-02A2_2x01_P4.20mm_Horizontal; LCSC C240832
J3, J13: Conn_01x06; PinHeader_1x06_P2.54mm_Vertical
J4, J5, J16, J17: XH-6AW; JST_XH_S6B-XH-A_1x06_P2.50mm_Horizontal; LCSC C8876
J6: XH-4AW; JST_XH_S4B-XH-A_1x04_P2.50mm_Horizontal; LCSC C21273
J7, J10: XH-10AW; JST_XH_S10B-XH-A_1x10_P2.50mm_Horizontal; LCSC C14652
J8, J9: 7-967288-1; TE_7-967288-1; Mouser Part Number 571-7-967288-1
J11, J12: XH-10A; JST_XH_B10B-XH-A_1x10_P2.50mm_Vertical; LCSC C8885
J14, J15: XH-6A; JST_XH_B6B-XH-A_1x06_P2.50mm_Vertical; LCSC C5663
J18: XH-8A; JST_XH_B8B-XH-A_1x08_P2.50mm_Vertical; LCSC C10385
J19: XH-8AW; JST_XH_S8B-XH-A_1x08_P2.50mm_Horizontal; LCSC XH-8AW
M1, M3: Module-wbo-0.3; wbo
M2, M4: Module-can-0.1; can
P1, P2, P3, P4, P5, P6, P7, P8, P9, P10, P11, P12, P13, P14, P15, P16, P17, P18, P19, P20, P21, P22, P23, P24, P25, P26, P27, P28, P29, P30, P31, P32, P33, P34, P35, P36, P37, P38, P39, P40, P41, P42, P43, P44, P45, P46, P47, P48, P49, P50, P51, P52, P53, P54, P55, P56, P57, P58, P59, P60, P61, P62, P63, P64, P65, P66, P67, P68, P69, P70, P71, P72, P73, P74, P75, P76, P77, P78, P79: Pad; PAD-TH
Q1, Q2: ISL9V3040S3S; TO-263-2; LCSC C898702
R1, R3: 22; R0603; LCSC C23345
R2, R4: DNP; R_2512_6332Metric
R5, R6: 51k; R0603; LCSC C23196
U1: MPXxx6115A; MPX_SOP_SSOP
U2: MPX4/MPXH6400_MAP; MPX-4_MAP

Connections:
+5VA: BRD1.C9 (5V_1), BRD1.C21 (5V_1), BRD1.C32 (5V_1), C1.2, C3.2, G5.6, G5.7, G5.8, G5.9, G5.10, J4.1, J4.2, J5.1, J5.2, J6.1, J18.1, J19.1, M1.W1 (V5_IN), M2.V1 (V5), M3.W1 (V5_IN), M4.V1 (V5), U1.2 (Vs), U2.3 (VCC)
/12V_MR: BRD1.B23 (12V_MR), F1.2, J7.1, J7.2, J10.1, J10.2, J11.1, J11.2, J12.1, J12.2
/12V_PROT: BRD1.C11 (12V_PROT), G5.11, G5.12, G5.13, G5.14, G5.15, P73.1
/12V_RAW: BRD1.B18 (12V_IGN), F4.2
/CAN_H: BRD1.B17 (CAN+), M2.S2 (CANH), M4.S2 (CANH)
/CAN_L: BRD1.B16 (CAN-), M2.S1 (CANL), M4.S1 (CANL)
/ETB1+: BRD1.B7 (ETB1+), J1.2
/ETB1-: BRD1.B6 (ETB1-), J1.1
/ETB2+: BRD1.B15 (ETB2+), J2.2
/ETB2-: BRD1.B8 (ETB2-), J2.1
/GATE_IGN1: BRD1.A35 (IGN1), J14.6, J16.6, P67.1, R1.2, R2.1
/GATE_IGN2: BRD1.A34 (IGN2), J14.5, J16.5, P49.1
/GATE_IGN3: BRD1.A22 (IGN3), J14.4, J16.4, P50.1
/GATE_IGN4: BRD1.A33 (IGN4), J14.3, J16.3, P51.1
/GATE_IGN5: BRD1.A32 (IGN5), J14.2, J16.2, P52.1
/GATE_IGN6: BRD1.A31 (IGN6), J14.1, J16.1, P53.1
/GATE_IGN7: BRD1.A30 (IGN7), J15.6, J17.6, P68.1, R3.2, R4.1
/GATE_IGN8: BRD1.A29 (IGN8), J15.5, J17.5, P54.1
/GATE_IGN9: BRD1.A28 (IGN9), J15.4, J17.4, P55.1
/GATE_IGN10: BRD1.A27 (IGN10), J15.3, J17.3, P56.1
/GATE_IGN11: BRD1.A26 (IGN11), J15.2, J17.2, P57.1
/GATE_IGN12: BRD1.A25 (IGN12), J15.1, J17.1, P58.1
/HV1: F2.1, J9.E3
/HV2: F3.1, J9.E6
/HV3: F5.1, J9.E9
/HV4: F6.1, J8.E3
/HV5: F7.1, J8.E6
/HV6: F8.1, J8.E9
/IN_AV10: BRD1.C28 (AV10), J18.2, J19.2
/IN_BARO: BRD1.C13 (AV1), C2.2, R5.1, U1.4 (Vout)
/IN_CAM: BRD1.B1 (D2), J9.C20
/IN_CLT: BRD1.C31 (AT4), J9.C22
/IN_CRANK+: BRD1.B5 (VR1+), J9.C32
/IN_CRANK-: BRD1.B13 (VR1-), J9.C46
/IN_D4: BRD1.B3 (D4), J18.6, J19.6
/IN_D5: BRD1.B9 (D5), J18.7, J19.7
/IN_IAT: BRD1.C30 (AT2), J8.C34
/IN_KNOCK1: BRD1.C34 (KNOCK1), J9.C49
/IN_KNOCK2: BRD1.C35 (KNOCK2), J9.C36
/IN_MAF1: BRD1.C17 (AV9), J9.C23
/IN_MAF2: BRD1.C18 (AV11), J8.C23
/IN_MAP: BRD1.C27 (AV8), C4.2, R6.1, U2.1 (VOUT)
/IN_PPS1: BRD1.C26 (AV6), J6.2
/IN_PPS2: BRD1.C16 (AV7), J6.3
/IN_START_BTN: BRD1.B2 (D3), J18.5, J19.5
/IN_TPS1_1: BRD1.C24 (AV2), J5.3
/IN_TPS1_2: BRD1.C14 (AV3), J5.4
/IN_TPS2_1: BRD1.C25 (AV4), J4.3
/IN_TPS2_2: BRD1.C15 (AV5), J4.4
/OUT_FAN_RELAY: BRD1.A12 (LS15), J18.3, J19.3
/OUT_FUEL_PUMP: BRD1.A23 (LS16), J18.4, J19.4
/OUT_IGN1: F2.2, F3.2, F5.2, Q1.2 (C), R2.2
/OUT_IGN7: F6.2, F7.2, F8.2, Q2.2 (C), R4.2
/OUT_INJ1: BRD1.A3 (LS1), J9.C41
/OUT_INJ2: BRD1.A15 (LS2), J9.C15
/OUT_INJ3: BRD1.A4 (LS3), J9.C40
/OUT_INJ4: BRD1.A16 (LS4), J9.C2
/OUT_INJ5: BRD1.A5 (LS5), J9.C28
/OUT_INJ6: BRD1.A6 (LS6), J9.C27
/OUT_INJ7: BRD1.A7 (LS7), J8.C41
/OUT_INJ8: BRD1.A19 (LS8), J8.C15
/OUT_INJ9: BRD1.A8 (LS9), J8.C40
/OUT_INJ10: BRD1.A20 (LS10), J8.C2
/OUT_INJ11: BRD1.A9 (LS11), J8.C28
/OUT_INJ12: BRD1.A21 (LS12), J8.C27
/OUT_MAIN_RELAY: BRD1.A10 (LS13), J9.B23
/OUT_STARTER_EN: BRD1.A11 (LS14), J9.D40
GND: BRD1.A17 (GND), BRD1.A18 (GND), BRD1.A24 (GND), BRD1.B14 (GND), BRD1.B19 (GND), BRD1.B20 (GND), BRD1.C1 (GND_SENS), BRD1.C2 (GND_SENS), BRD1.C3 (GND_SENS), BRD1.C4 (GND_SENS), BRD1.C5 (GND_SENS), BRD1.C6 (GND_SENS), BRD1.C7 (GND_SENS), BRD1.C8 (GND_SENS), BRD1.C23 (GND_SENS), BRD1.C29 (GND_SENS), C1.1, C2.1, C3.1, C4.1, G5.1, G5.2, G5.3, G5.4, G5.5, J3.3, J4.5, J4.6, J5.5, J5.6, J6.4, J7.9, J7.10, J8.A4, J8.A6, J8.C6, J8.C9, J8.C19, J8.C37, J8.C45, J8.C47, J8.C50, J8.E1, J8.E5, J9.A4, J9.A6, J9.C6, J9.C9, J9.C21, J9.C37, J9.C45, J9.C50, J9.E1, J9.E5, J10.9, J10.10, J11.9, J11.10, J12.9, J12.10, J13.3, J18.8, J19.8, M1.E6 (LSU_H-), M1.G (GND), M2.E1 (GND), M3.E6 (LSU_H-), M3.G (GND), M4.E1 (GND), Q1.3 (E), Q2.3 (E), R5.2, R6.2, U1.3 (GND), U2.2 (GND)
unnamed: BRD1.A1 (HS2), P46.1
unnamed: BRD1.A2 (HS1), P45.1
unnamed: BRD1.A13 (HS3), P47.1
unnamed: BRD1.A14 (HS4), P48.1
unnamed: BRD1.B4 (VR2+), P63.1
unnamed: BRD1.B10 (D1), P59.1
unnamed: BRD1.B11 (D6), P62.1
unnamed: BRD1.B12 (VR2-), P64.1
unnamed: BRD1.B21 (CAN2-), P66.1
unnamed: BRD1.B22 (CAN2+), P65.1
unnamed: BRD1.C12 (12V_PROT), P74.1
unnamed: BRD1.C19 (AT1), P70.1
unnamed: BRD1.C20 (AT3), P71.1
unnamed: F1.1, J9.A8
unnamed: F4.1, J9.D26
unnamed: G1.1, G1.6, G1.11
unnamed: G1.5, G1.10, G1.15
unnamed: G1.2, G1.7, G1.12
unnamed: G1.3, G1.8, G1.13
unnamed: G1.4, G1.9, G1.14
unnamed: G2.1, G2.6, G2.11
unnamed: G2.5, G2.10, G2.15
unnamed: G2.2, G2.7, G2.12
unnamed: G2.3, G2.8, G2.13
unnamed: G2.4, G2.9, G2.14
unnamed: G3.1, G3.6, G3.11
unnamed: G3.5, G3.10, G3.15
unnamed: G3.2, G3.7, G3.12
unnamed: G3.3, G3.8, G3.13
unnamed: G3.4, G3.9, G3.14
unnamed: G4.1, G4.6, G4.11
unnamed: G4.5, G4.10, G4.15
unnamed: G4.2, G4.7, G4.12
unnamed: G4.3, G4.8, G4.13
unnamed: G4.4, G4.9, G4.14
unnamed: G6.1, G6.6, G6.11
unnamed: G6.5, G6.10, G6.15
unnamed: G6.2, G6.7, G6.12
unnamed: G6.3, G6.8, G6.13
unnamed: G6.4, G6.9, G6.14
unnamed: G7.1, G7.6, G7.11
unnamed: G7.5, G7.10, G7.15
unnamed: G7.2, G7.7, G7.12
unnamed: G7.3, G7.8, G7.13
unnamed: G7.4, G7.9, G7.14
unnamed: J3.1, M3.W8 (V33_OUT)
unnamed: J3.2, M3.W7 (SWCLK)
unnamed: J3.4, M3.W6 (SWDIO)
unnamed: J3.5, M3.W5 (nReset)
unnamed: J8.A7, P28.1
unnamed: J8.A8, P29.1
unnamed: J8.B3, P1.1
unnamed: J8.B4, P17.1
unnamed: J8.B5, P34.1
unnamed: J8.B7, P60.1
unnamed: J8.B8, P61.1
unnamed: J8.B9, P69.1
unnamed: J8.B10, P72.1
unnamed: J8.B11, P75.1
unnamed: J8.B15, P76.1
unnamed: J8.B17, P77.1
unnamed: J8.B19, P78.1
unnamed: J8.B23, P79.1
unnamed: J8.C3, P30.1
unnamed: J8.C14, P31.1
unnamed: J8.C18, P32.1
unnamed: J8.C20, P33.1
unnamed: J8.C32, P35.1
unnamed: J8.C36, P36.1
unnamed: J8.C46, P37.1
unnamed: J8.C49, P38.1
unnamed: J8.D6, P39.1
unnamed: J8.D10, P40.1
unnamed: J8.D26, P41.1
unnamed: J8.D36, P42.1
unnamed: J8.D37, P43.1
unnamed: J8.D40, P44.1
unnamed: J9.A7, P2.1
unnamed: J9.B3, P3.1
unnamed: J9.B4, P4.1
unnamed: J9.B7, P5.1
unnamed: J9.B8, P6.1
unnamed: J9.B9, P7.1
unnamed: J9.B10, P8.1
unnamed: J9.B11, P9.1
unnamed: J9.B15, P10.1
unnamed: J9.B17, P11.1
unnamed: J9.B18, P12.1
unnamed: J9.B19, P13.1
unnamed: J9.C3, P14.1
unnamed: J9.C14, P15.1
unnamed: J9.C18, P16.1
unnamed: J9.C52, P18.1
unnamed: J9.D3, P19.1
unnamed: J9.D6, P20.1
unnamed: J9.D10, P21.1
unnamed: J9.D17, P22.1
unnamed: J9.D29, P23.1
unnamed: J9.D30, P24.1
unnamed: J9.D34, P25.1
unnamed: J9.D36, P26.1
unnamed: J9.D37, P27.1
unnamed: J10.3, J12.3, M3.E1 (LSU_Un)
unnamed: J10.4, J12.4, M3.E2 (LSU_Vm)
unnamed: J10.5, J12.5, M3.E3 (LSU_Ip)
unnamed: J10.6, J12.6, M3.E4 (LSU_Rtrim)
unnamed: J10.7, J10.8, J12.7, J12.8, M3.E5 (LSU_H+)
unnamed: J7.3, J11.3, M1.E1 (LSU_Un)
unnamed: J7.4, J11.4, M1.E2 (LSU_Vm)
unnamed: J7.5, J11.5, M1.E3 (LSU_Ip)
unnamed: J7.6, J11.6, M1.E4 (LSU_Rtrim)
unnamed: J7.7, J7.8, J11.7, J11.8, M1.E5 (LSU_H+)
unnamed: J13.1, M1.W8 (V33_OUT)
unnamed: J13.2, M1.W7 (SWCLK)
unnamed: J13.4, M1.W6 (SWDIO)
unnamed: J13.5, M1.W5 (nReset)
unnamed: M1.J2 (SEL2), M1.J_VCC2 (PULL_UP2)
unnamed: M1.W2 (CAN_VIO), M4.V2 (CAN_VIO)
unnamed: M1.W3 (CAN_RX), M4.V6 (CAN_RX)
unnamed: M1.W4 (CAN_TX), M4.V5 (CAN_TX)
unnamed: M2.V2 (CAN_VIO), M3.W2 (CAN_VIO)
unnamed: M2.V5 (CAN_TX), M3.W4 (CAN_TX)
unnamed: M2.V6 (CAN_RX), M3.W3 (CAN_RX)
unnamed: M3.J1 (SEL1), M3.J_GND1 (PULL_DOWN1)
unnamed: Q1.1 (G), R1.1
unnamed: Q2.1 (G), R3.1

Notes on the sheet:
BLACK
CAN?
GRAY
Connectors 776228-1 776231-1 776231-2 Mating plugs 770680-1 776164-1 776164-2 Terminals 770854-1 all of the above cheap from ttiinc.com
TODO: Add "baro" silkscreen
For MPXH6400

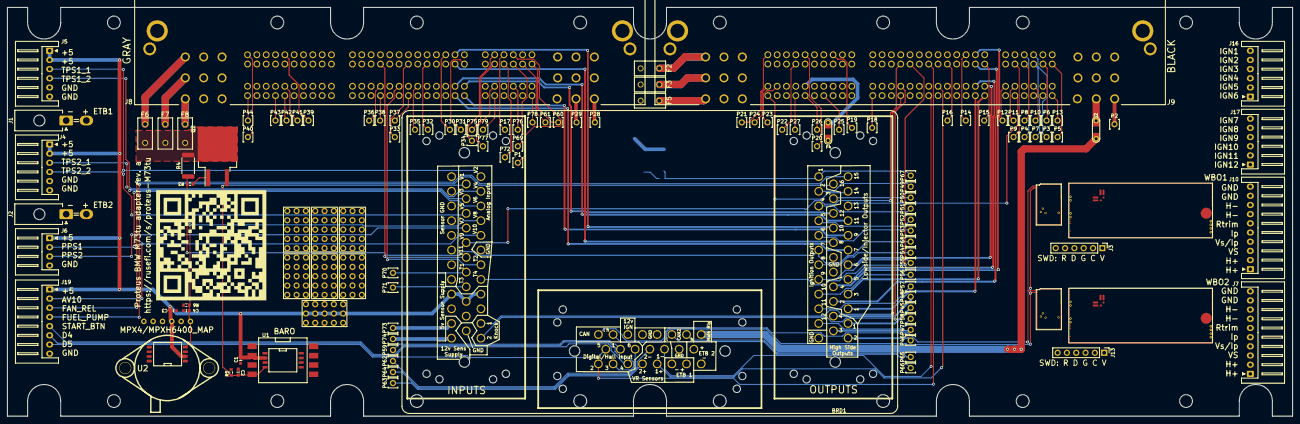
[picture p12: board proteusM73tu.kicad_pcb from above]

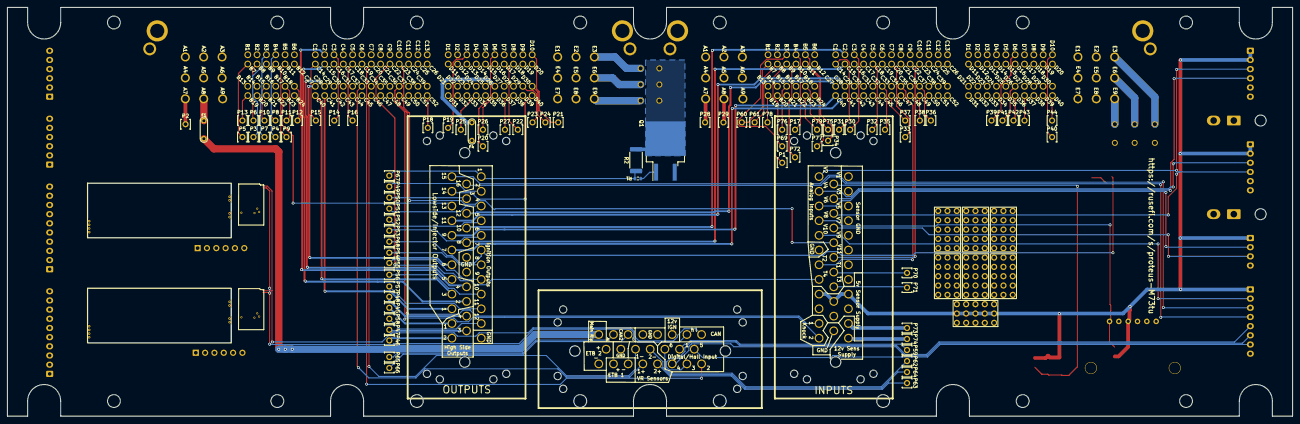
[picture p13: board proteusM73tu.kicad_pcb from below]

Board: 2 copper layers, 350.0 x 111.3 mm, 127 parts (3 on the bottom side), 194 nets.

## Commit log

2021-09-21 random files
    [Breakout_134pin_with_igniter.kicad_pcb, Breakout_134pin_with_igniter.sch]
2021-09-26 Placed connectors
    [proteusM73tu.kicad_pcb, proteusM73tu.kicad_sch]
2021-09-29 ETB pins drama
    [proteusM73tu.kicad_sch]
2021-10-04 Upd pinout
    [proteusM73tu.kicad_pcb, proteusM73tu.kicad_sch]
2021-10-04 Upd sch
    [proteusM73tu.kicad_pcb, proteusM73tu.kicad_sch]
2021-10-24 Upd PCB
    [proteusM73tu.kicad_pcb, proteusM73tu.kicad_sch]
2021-10-25 Fab preview
    [M73tu-BOM.csv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]
2021-10-26 dead stuff
    [Breakout_134pin_with_igniter.kicad_pcb, Breakout_134pin_with_igniter.sch]
2021-10-26 Board size
